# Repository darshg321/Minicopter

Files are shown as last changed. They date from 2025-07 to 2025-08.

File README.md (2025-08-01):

# Minicopter

A lightweight ESP-32 based drone capable of autonomous pathing, built for agility. Uses the GY-87 breakout board with a three-axis gyroscope + triaxial accelerometer + three-axis magnetic field + pressure. Charges a LiPo battery with USB-C and can be flashed with firmware.
Can be controlled with both pathing commands and bluetooth controls.

I made this project after getting inspiration from a different esp32 drone reel, and thought I could make that too
I've additionally always wanted to get into creating a from-scratch hardware project that includes microcontrollers and pcbs, and thought this was the perfect place to start

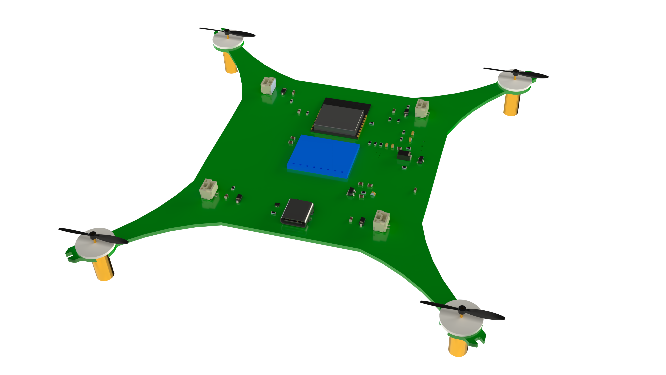
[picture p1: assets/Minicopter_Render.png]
cad


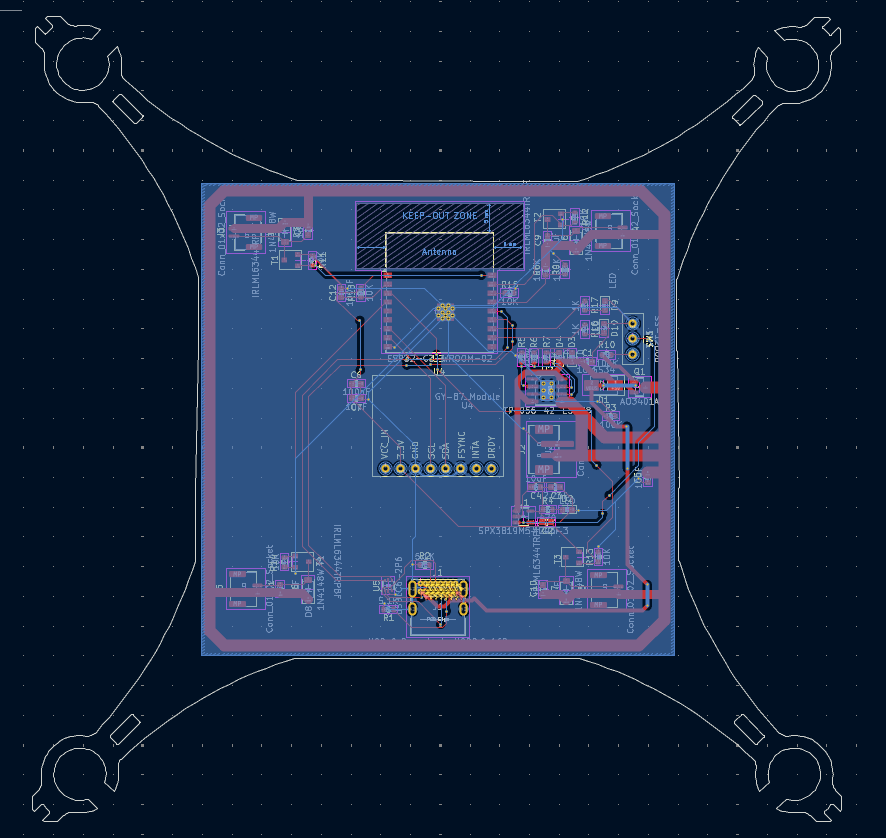
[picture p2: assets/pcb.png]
pcb


## Read the [JOURNAL.md](JOURNAL.md)

# BOM

| Value | Qty | Price (USD, approx) |
|---|-----|---|
| 10uF | 3 | 0.46 |
| 470pF | 1 | 0.4 |
| 2.2uF | 1 | 0.19 |
| 100nF | 2 | 0.14 |
| 10nF | 1 | 0.09 |
| 1uF | 4 | 0.05 |
| SS34 | 1 | 0.66 |
| LED | 5 | 1.39 |
| 1N4148W | 4 | 0.77 |
| USB_C_Receptacle_USB2.0_16P | 1 | 0.88 |
| Conn_01x02 | 1 | 1.39 |
| Conn_01x02_Socket | 4 | 0.70 |
| AO3401A | 1 | 0.46 |
| 5.1K | 2 | 0.45 |
| 100K | 4 | 0.2 |
| 470 | 1 | 0.28 |
| 1.2K | 1 | 0.61 |
| 1K | 4 | 0.2 |
| 10K | 6 | 0.19 |
| SS-12D00 | 1 | 1.39 |
| IRLML6344TRPBF | 4 | 1.08 |
| SPX3819M5-L-3-3 | 1 | 0.46 |
| TP4056-42-ESOP8 | 1 | 1.73 |
| ESP32-C3-WROOM-02 | 1 | 3.28 |
| GY-87_Module | 1 | 3.00 |
| USBLC6-2P6 | 1 | 0.46 |
| 3.7V 500mAh 902530 25C LiPo Battery | 3 | 12.68 |
| NewBeeDrone BDR Unicorn Edition Motors - 6mm Brushed Motors | 1 | 19.99 |
| NewBeeDrone Venom V2 Super Durable Propellers | 1 | 2.99 |
| Total (w/ shipping + tax) | | 138.15 |

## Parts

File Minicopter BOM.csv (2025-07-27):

Reference | Value | Footprint | Qty |  | Price (w/o shipping + taxes USD)
C1, C4, C5 | 10uF | Capacitor_SMD:C_0603_1608Metric | 3 | https://www.digikey.ca/en/products/detail/taiyo-yuden/LMK107BBJ106MALT/3662195 | 0.46
C2 | 470pF | Capacitor_SMD:C_0603_1608Metric | 1 | https://www.digikey.ca/en/products/detail/kemet/C0603C471J5GACTU/2200803 | 0.4
C3 | 2.2uF | Capacitor_SMD:C_0603_1608Metric | 1 | https://www.digikey.ca/en/products/detail/taiyo-yuden/TMK107ABJ225KA-T/2648986 | 0.19
C6, C12 | 100nF | Capacitor_SMD:C_0603_1608Metric | 2 | https://www.digikey.ca/en/products/detail/yageo/CC0603KRX7R7BB104/302822 | 0.14
C7 | 10nF | Capacitor_SMD:C_0603_1608Metric | 1 | https://www.digikey.ca/en/products/detail/kemet/C0603C103K5RACTU/411090 | 0.09
C8, C9, C10, C11 | 1uF | Capacitor_SMD:C_0603_1608Metric | 4 | https://www.digikey.ca/en/products/detail/samsung-electro-mechanics/CL10B105KP8NNNC/3887604 | 0.05
D1 | SS34 | Diode_SMD:D_SMA | 1 | https://www.digikey.ca/en/products/detail/onsemi/SS34/1052384 | 0.66
D2, D3, D4, D9, D10 | LED | LED_SMD:LED_0603_1608Metric | 5 | https://www.aliexpress.com/item/1005005431944057.html | 1.39
D5, D6, D7, D8 | 1N4148W | Diode_SMD:D_SOD-123 | 4 | https://www.digikey.ca/en/products/detail/smc-diode-solutions/1N4148W/6022450 | 0.77
J1 | USB_C_Receptacle_USB2.0_16P | Connector_USB:USB_C_Receptacle_GCT_USB4085 | 1 | https://www.digikey.ca/en/products/detail/gct/USB4085-GF-A/98596622 | 0.88
J2 | Conn_01x02 | Connector_JST:JST_PH_B2B-PH-SM4-TB_1x02-1MP_P2.00mm_Vertical | 1 | https://www.aliexpress.com/item/1005008131930144.html | 1.39
J3, J4, J5, J6 | Conn_01x02_Socket | Connector_JST:JST_GH_BM02B-GHS-TBT_1x02-1MP_P1.25mm_Vertical | 4 | https://www.aliexpress.com/item/1005005699355153.html | 0.7
Q1 | AO3401A | Package_TO_SOT_SMD:SOT-23 | 1 | https://www.digikey.ca/en/products/detail/alpha-omega-semiconductor-inc/AO3401A/1855773 | 0.46
R1, R2 | 5.1K | Resistor_SMD:R_0603_1608Metric | 2 | https://www.digikey.ca/en/products/detail/yageo/RC0603FR-075K1L/727268 | 0.45
R3, R8, R9, R10 | 100K | Resistor_SMD:R_0603_1608Metric | 4 | https://www.digikey.ca/en/products/detail/stackpole-electronics-inc/RMCF0603FT100K/1761112 | 0.2
R4 | 470 | Resistor_SMD:R_0603_1608Metric | 1 | https://www.digikey.ca/en/products/detail/te-connectivity-passive-product/CRGCQ0603F470R/8576286 | 0.28
R5 | 1.2K | Resistor_SMD:R_0603_1608Metric | 1 | https://www.digikey.ca/en/products/detail/panasonic-electronic-components/ERA-3AEB122V/14658566 | 0.61
R6, R7, R16, R17 | 1K | Resistor_SMD:R_0603_1608Metric | 4 | https://www.digikey.ca/en/products/detail/stackpole-electronics-inc/RMCF0603FT1K00/1761077 | 0.2
R11–R15, R18 | 10K | Resistor_SMD:R_0603_1608Metric | 6 | https://www.digikey.ca/en/products/detail/stackpole-electronics-inc/RMCF0603JT10K0/1758104 | 0.19
SW1 | SS-12D00 | SS-12D00:SS12-D00 | 1 | https://www.aliexpress.com/item/4001187999740.htmll | 1.39
T1, T2, T3, T4 | IRLML6344TRPBF | IRLML6344TRPBF:IRLML6344TRPBF | 4 | https://www.aliexpress.com/item/1005005586173911.html | 1.08
U1 | SPX3819M5-L-3-3 | Package_TO_SOT_SMD:SOT-23-5 | 1 | https://www.digikey.ca/en/products/detail/maxlinear-inc/SPX3819M5-L-3-3-TR/2472394 | 0.46
U2 | TP4056-42-ESOP8 | Package_SO:SOIC-8-1EP_3.9x4.9mm_P1.27mm_EP2.41x3.3mm_ThermalVias | 1 | https://www.aliexpress.com/item/1005009057944694.html | 1.73
U3 | ESP32-C3-WROOM-02 | RF_Module:ESP32-C3-WROOM-02 | 1 | https://www.digikey.ca/en/products/detail/espressif-systems/ESP32-C3-WROOM-02-N4/145530311 | 3.28
U4 | GY-87_Module | GY-87_Module:GY-87_Module | 1 | https://www.aliexpress.com/i/32668253323.html | 3 |  | Total (USD)
U5 | USBLC6-2P6 | Package_TO_SOT_SMD:SOT-666 | 1 | https://www.digikey.ca/en/products/detail/stmicroelectronics/USBLC6-2SC6Y/2819177 | 0.46 | Subtotal | 58.21
 | 2.54mm Headers |  | 1 | https://www.digikey.ca/en/products/detail/amphenol-cs-fci/10129378-910002BLF/7915958 | 1.64 | NewBeeDrone | 24.17
 | 3.7V 500mAh 902530 25C LiPo Battery |  | 3 | https://www.aliexpress.com/item/1005007016796736.html | 12.68 | Digikey | 20
 | NewBeeDrone BDR Unicorn Edition Motors - 6mm Brushed Motors |  | 1 | https://newbeedrone.com/collections/drone-motors/products/newbeedrone-bdr-unicorn-edition-motors-6mm-brushed-motors | 19.99 | Aliexpress | 25.77
 | NewBeeDrone Venom V2 Super Durable Propellers 31mm -0.8mm Shaft |  | 1 | https://newbeedrone.com/collections/drone-propellers/products/newbeedrone-venom-v2-super-durable-propellers-31mm-0-8mm-shaft4ccw-4cw | 2.99 | Taxes | 10
 |  |  |  |  | 58.21 |  | 138.15

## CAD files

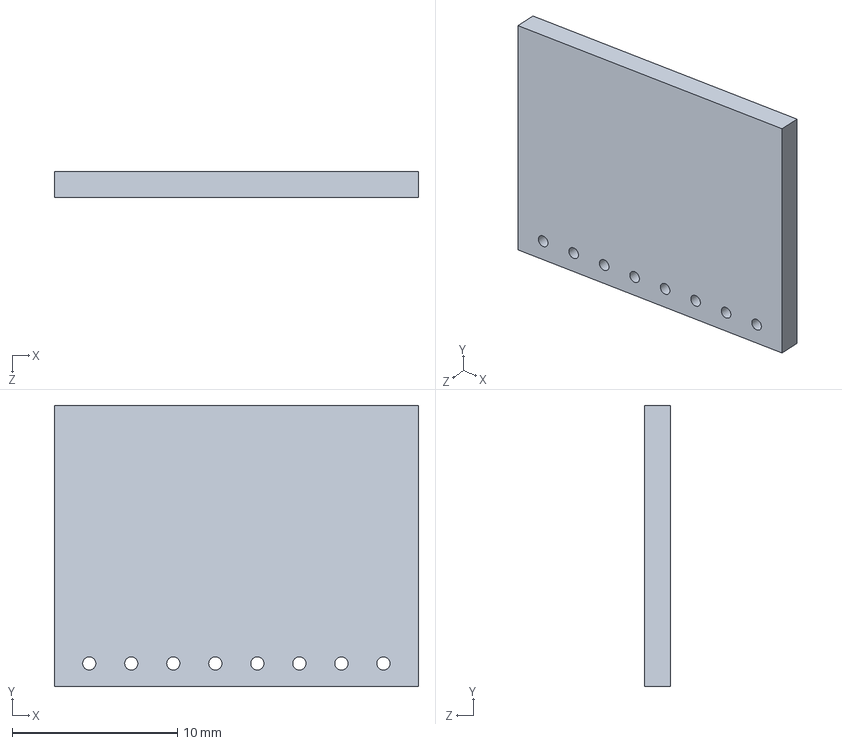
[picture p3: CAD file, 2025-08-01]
cad/GY-87.SLDPRT
22.0 x 17.0 x 1.60 mm

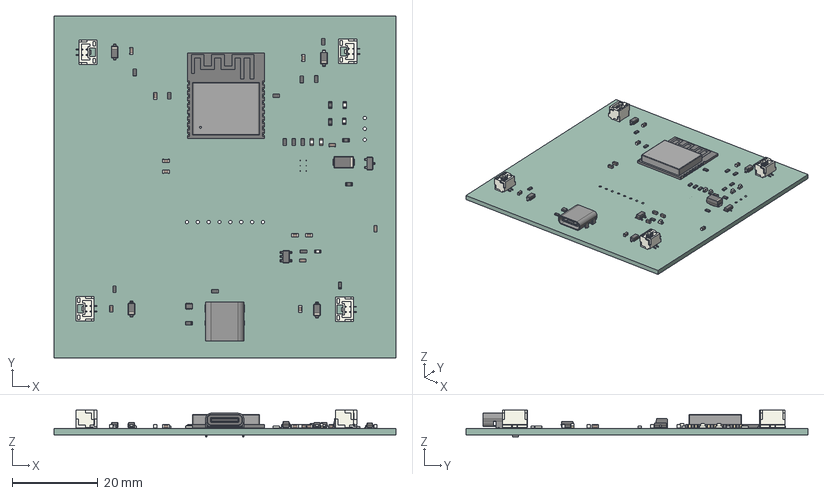
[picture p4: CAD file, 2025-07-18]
pcb/Minicopter.step
80.0 x 80.0 x 6.31 mm
D_SOD-123 x 4
JST_GH_BM02B-GHS-TBT_1x02-1MP_P1.25mm_Vertical x 4
R_0603_1608Metric x 18
ESP32-C3-WROOM-02
C_0603_1608Metric x 12
D_SMA
SOT-23-5
LED_0603_1608Metric x 5
SOT-666
SOT-23
USB_C_Receptacle_GCT_USB4085
Minicopter_PCB

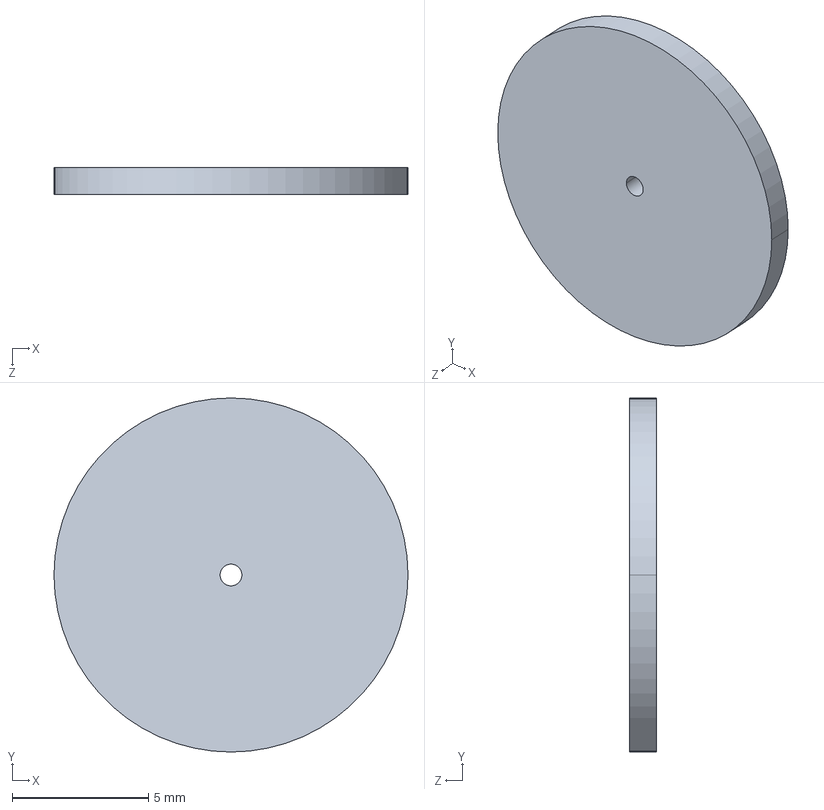
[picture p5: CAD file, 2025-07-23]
production/motor_attachment.STEP
13.0 x 13.0 x 1.00 mm

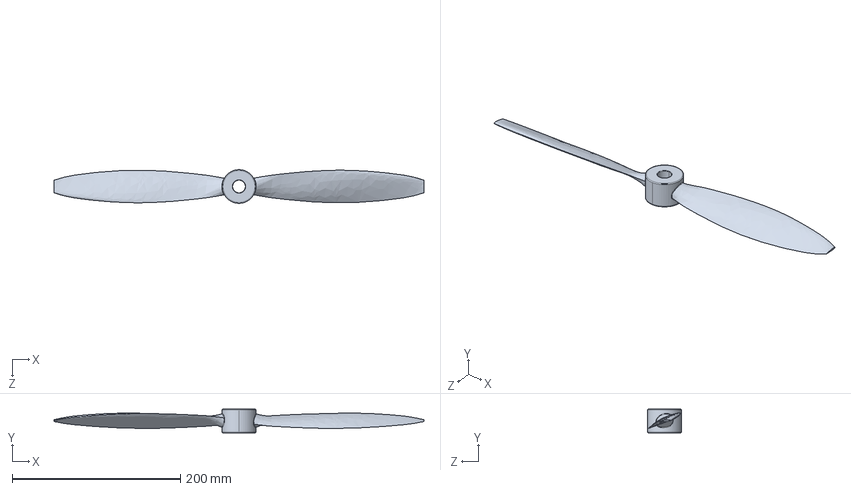
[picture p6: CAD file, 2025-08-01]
cad/BLDC Propeller.STEP
440.0 x 28.0 x 40.0 mm

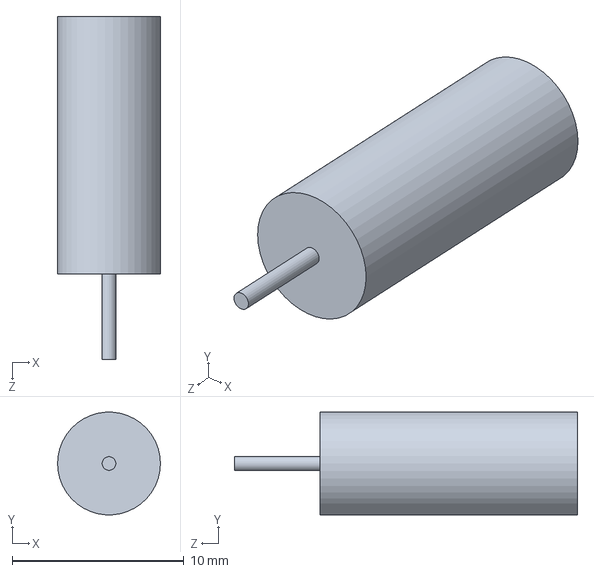
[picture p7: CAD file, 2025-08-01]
cad/Motor.SLDPRT
6.00 x 5.98 x 20.0 mm

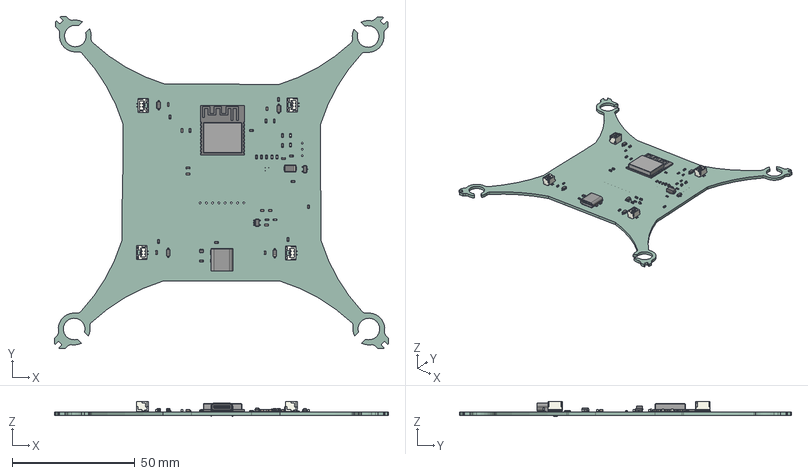
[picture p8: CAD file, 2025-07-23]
cad/Minicopter_PCB.step
136.1 x 135.4 x 6.31 mm
D_SOD-123 x 4
JST_GH_BM02B-GHS-TBT_1x02-1MP_P1.25mm_Vertical x 4
R_0603_1608Metric x 18
ESP32-C3-WROOM-02
C_0603_1608Metric x 12
D_SMA
SOT-23-5
LED_0603_1608Metric x 5
SOT-666
SOT-23
USB_C_Receptacle_GCT_USB4085
Minicopter_PCB

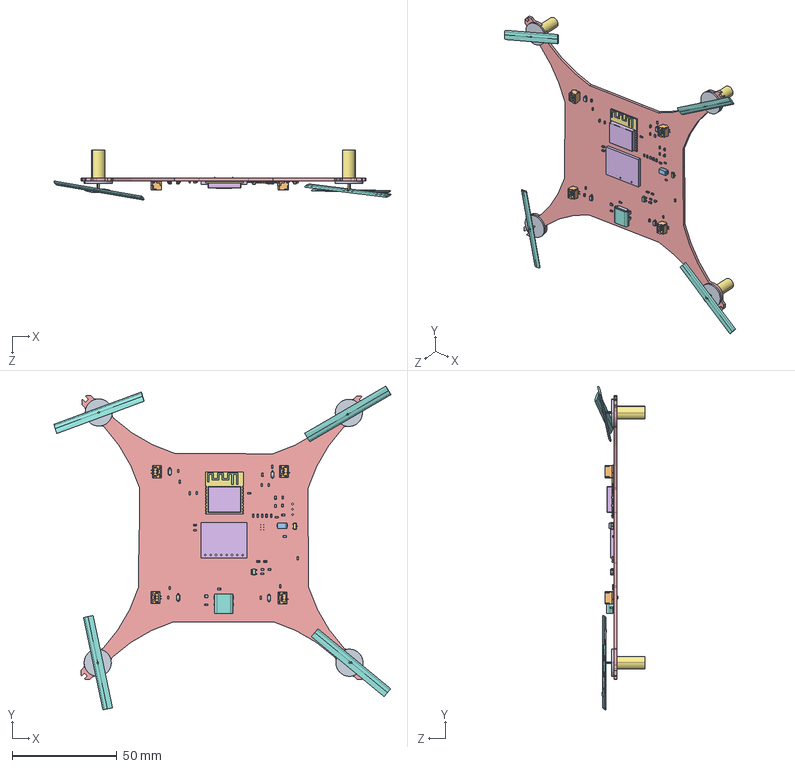
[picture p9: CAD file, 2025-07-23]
cad/Minicopter.STEP
160.8 x 154.4 x 24.1 mm
D_SOD-123 x 4
JST_GH_BM02B-GHS-TBT_1x02-1MP_P1.25mm_Vertical x 4
R_0603_1608Metric x 18
ESP32-C3-WROOM-02
C_0603_1608Metric x 12
D_SMA
SOT-23-5
LED_0603_1608Metric x 5
SOT-666
SOT-23
USB_C_Receptacle_GCT_USB4085
Minicopter_PCB
GY-87
Motor x 4
Propellers x 4
motor_attachment x 4

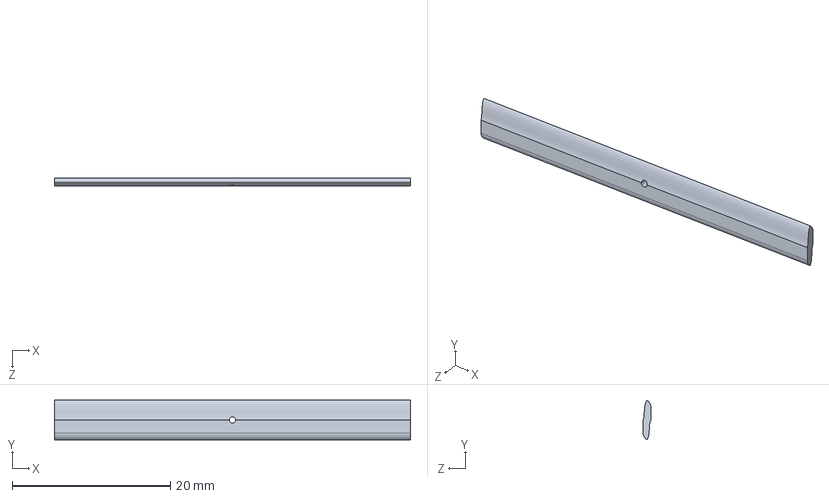
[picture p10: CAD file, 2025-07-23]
cad/Propellers.SLDPRT
45.0 x 5.00 x 1.00 mm

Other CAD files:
cad/motor_attachment.SLDPRT
cad/CirPattern1_1.SLDPRT
cad/USB_C_Receptacle_GCT_USB4085.SLDPRT
cad/D_SOD-123.SLDPRT
cad/SOT-23-5.SLDPRT
cad/C_0603_1608Metric.SLDPRT
cad/D_SMA.SLDPRT
cad/SOT-666.SLDPRT
cad/ESP32-C3-WROOM-02.SLDPRT
cad/JST_GH_BM02B-GHS-TBT_1x02-1MP_P1.25mm_Vertical.SLDPRT
cad/BLDC Propeller.SLDASM
cad/LED_0603_1608Metric.SLDPRT
cad/Minicopter.SLDASM
cad/Minicopter_PCB.SLDPRT
cad/R_0603_1608Metric.SLDPRT
cad/SOT-23.SLDPRT

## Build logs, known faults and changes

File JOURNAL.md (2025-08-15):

## time: 35 hours

## july 6 & 7

got inpsiration for this project from this reel: https://www.instagram.com/p/DKDFd3nS-c8/
other inspiration: https://circuitdigest.com/microcontroller-projects/DIY-wifi-controlled-drone

goals of this drone:

- can fly reliably
- wireless controller
- PID control
- 4 ish minute flight time
- usb c charging
- can have semi reliable autonomous paths (can create one to takeoff, fly from my room to couch, and land, reliably)

the guy uses NewBeeDrone BDR GOLD Edition - 6mm Brushed Motor, so i'll be basing my design off of these motors

shoutout to this blog article for being quite helpful in esp selection: https://eitherway.io/posts/esp32-buyers-guide/
i will go with the esp32-c3-wroom-02 for its bluetooth 5.0 and efficiency

parts v1:
NewBeeDrone BDR GOLD Edition - 6mm Brushed Motor (https://newbeedrone.com/products/newbeedrone-bdr-gold-edition-6mm-brushed-motor)
Bitcraze Crazyflie Nano Quadcopter Replacement Propellers (https://ca.robotshop.com/products/crazyflie-nano-quadcopter-replacement-propellers)
Fytoo 5pcs 3.7V 500mAh 25C Li Battery (https://www.amazon.ca/dp/B0794ZPVSX)
ESP32-C3 (https://www.digikey.ca/en/products/detail/espressif-systems/ESP32-C3/14115579)
GY-87 (https://x2robotics.ca/gy-87-10dof-mpu6050-hmc5883l-bmp180-sensor-module)
TYPE-C-31-M-12 (https://lcsc.com/product-detail/USB-Type-C_Korean-Hroparts-Elec-TYPE-C-31-M-12_C165948.html)
TP4056 (https://www.aliexpress.com/item/1005005838857868.html)
SPX3819M5-L-3-3 (https://www.aliexpress.com/item/1005007348027539.html)
IRLZ44N (https://www.aliexpress.com/item/1005006228628494.html)

- figure out how to implement tp4056 with battery protection or figure out if its not necessary
- figure out how to add breakout board to custom pcb

components left: motor driver, battery charge terminal, controller components (oled screen etc)

+4 hours; lot of research :( 

making a choice not to use usb uart bc im using esp32 c3 and will just use the native usb support

# schematics:

## july 8th

components:
usb_c_receptable_usb2.0_16p
AO3401A
SS34
SPX3819M5-L-3-3
4 capacitors, 3 resistors, and 1 led

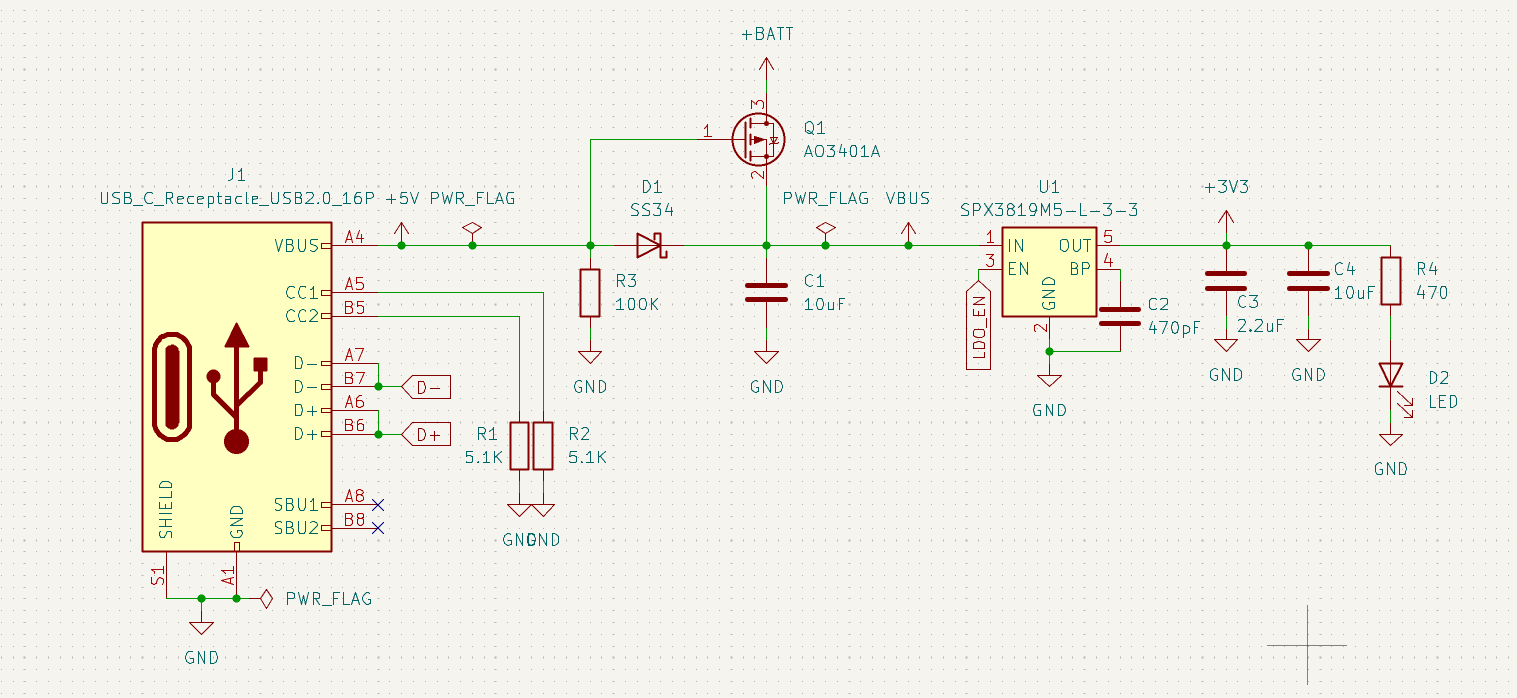
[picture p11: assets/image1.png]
power


circuit explanation for later me:
- cc1 and cc2 have resistors to let chargers know to supply power, not take in power
- vbus is 5v, the goal of the circuit is to convert it into stable 3v
- power goes to ss34 where cathode is toward vbus, prevents reverse current
- r3 ensures mosfet is on when usb isnt connected due to gnd connection, and turns mosfet off when usb is connected
- ao3401A (mosfet) allows for battery power when usb isnt connected
- EN is to turn the ldo on, which acts as the power switch for the entire device
- BP is for noise reduction, adding a capacitor does this
- two more capaicitors to add stabalization on the 3v3 rail, connected in parallel and will supply voltage in drops
- green led for on status

components:
TP4056
2 resistor, 3 resistor, 1 capacitor
51005-0200 molex female housing

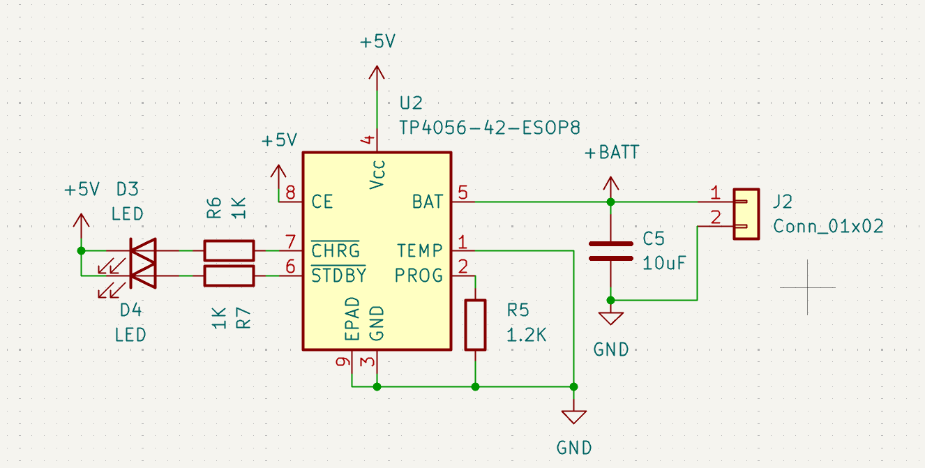
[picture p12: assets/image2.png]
battery


circuit explanation: 
- power comes from vcc
- ce turns on charging, connected to 5v so always charging
- epad is for cooling
- temp is for temp monitoring (not doing that)
- prog is to set charging amps (1amp at 1.2k resistor)
- capicitor smooths out charging

third schematic: on/off and voltage monitoring (battery control)

components:
3 resistors
MST22D18G2_125 (https://www.amazon.ca/100Pcs-MSS22D18-Miniature-Switch-Handle/dp/B093LBLK6D)

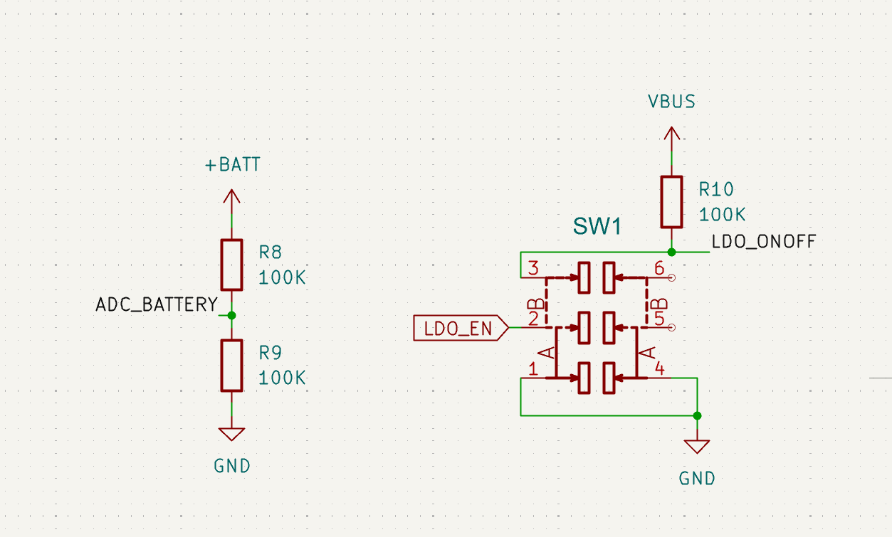
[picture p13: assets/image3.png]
batterycontrol


+6 hours

## july 9th

circuit explanation:
- battery capacity is measured by the voltage divider, linking to an adc pin
- when switch is toggled, it either connects ldo's en to gnd (off), or to vbus via r10
- r10 is there to not short the circuit when untoggled (pull up resistor)

fourth schematic: microcontroller

components: 
- esp32-c3-wroom-02
- 2 resistor, 1 capacitor

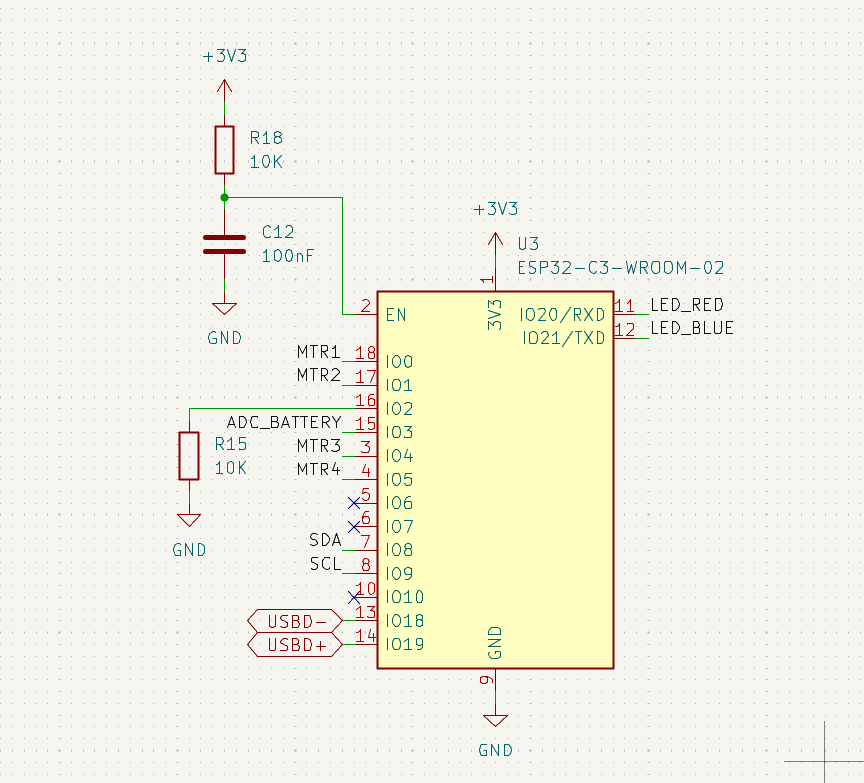
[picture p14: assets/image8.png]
microcontroller


circuit explanation:
- en must be HIGH to boot, pull up resistor and capacitor for stability
- io2 is for boot and optionally has a pull down resistor
- io6, 7, and 10 are for firmware and cannot be connected
- io20/21 are rxd and txd and supposed to be for uart serial communication, but since im using native usb ill be controlling leds with them
- io3 works for adc
- io18/19 are usb for the esp32-c3-wroom-02

fifth schematic: sensor
unfortunately the mpu6050 seems to only be in qfn form (and discontinued) and since i dont have the tools to solder that, i'll be using the gy-87 module
links that are helpful w this:
https://docs.sunfounder.com/projects/elite-explorer-kit/en/latest/basic_projects/09_basic_gy87.html
https://www.reddit.com/r/PrintedCircuitBoard/comments/b704j7/how_to_connect_breakout_board_with_a_pcb/
https://electropeak.com/learn/interfacing-gy-87-10dof-imu-mpu6050-hmc5883l-bmp085-module-with-arduino/
https://5.imimg.com/data5/LF/FE/MY-1833510/gy-87-10dof-mpu6050-hmc5883l-bmp180-sensor-module.pdf

gy87 symbol: 
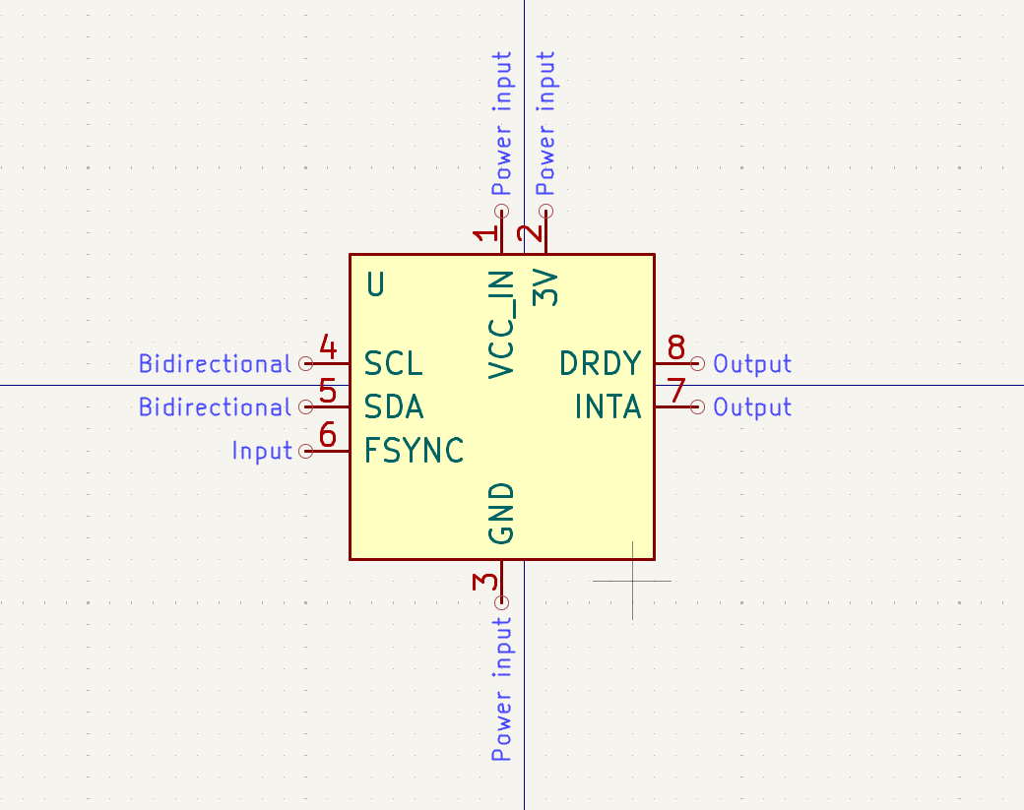
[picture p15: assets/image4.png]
gy87 symbol


components:
- gy87
- 2 capacitor

connections:
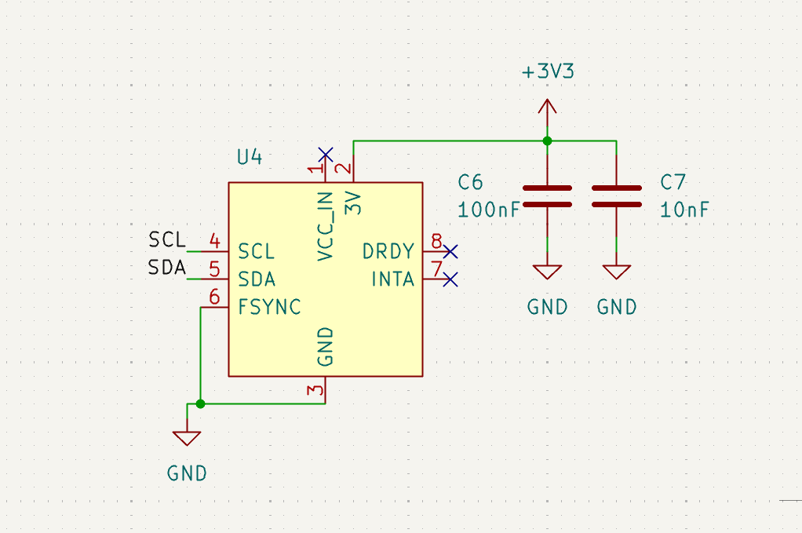
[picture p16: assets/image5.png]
sensor


circuit explanation:
- scl and sda go to the pins on esp32, dont need pull up resistors or 3v because the breakout board already has that
- dont use vcc_in, drdy, and inta
- fsync connects to gnd because its an output pin unlike the other input pins, and so may pick up on random noise and so has to be connected to gnd
- breakout board likely already has decoupling capacitors for the power, but might as well add them anyways for ensured reliability

+6 hours

## july 10th

sixth schematic: motor drivers

components:
- 4 IRLML6344TRPBF
- 4 resistor
- 4 1N414BW

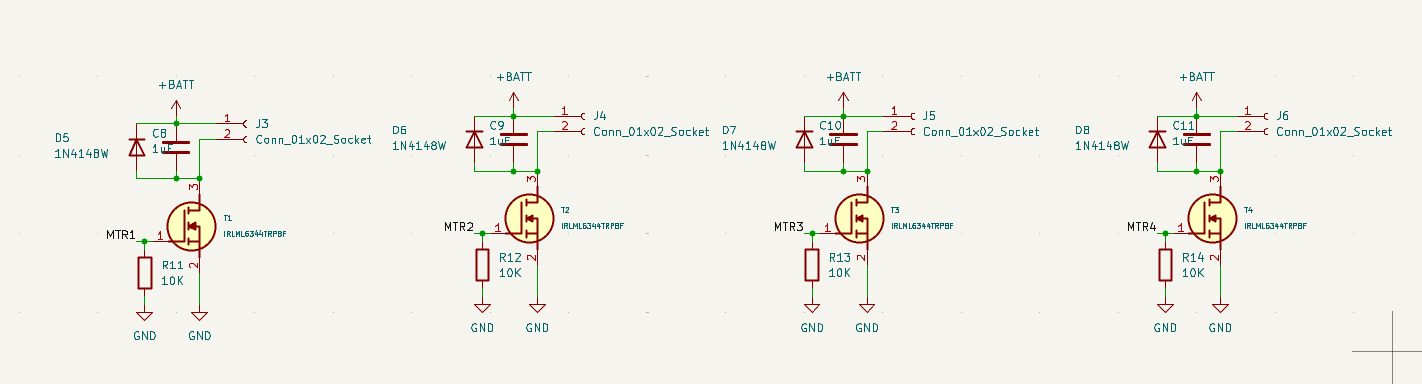
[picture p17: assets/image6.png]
motor drivers


circuit explanation:
- pin 1 is the gate on the mosfet, pin 3 is the drain, pin 2 is the source
- when pin 1 of the mosfet is turned on by the microcontroller, the switch is on and the current can flow from the battery to gnd
- this allows the motor to spin because it connects the motors negative terminal to gnd
- when the mosfet is closed, the motor cannot spin because it only has positive terminal plugged into the battery

seventh schematic: status leds

components:
- 2 leds
- 2 resistors

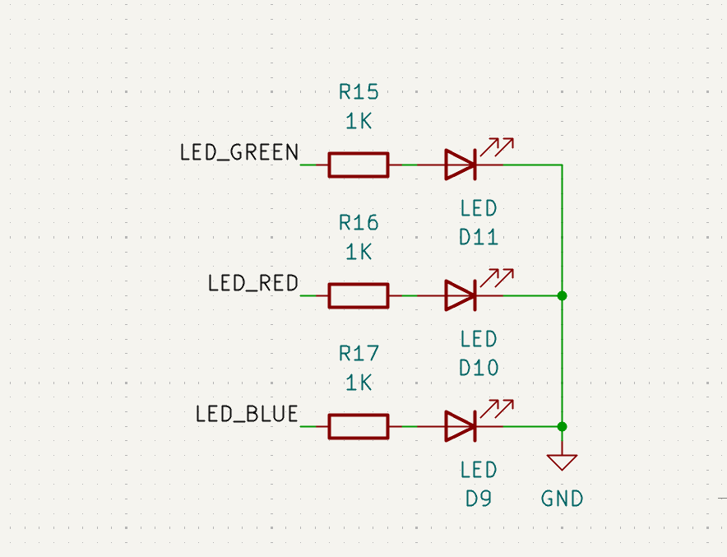
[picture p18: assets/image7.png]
status leds


finished
now for errors :(
fixed errors, apparently net labels dont work across sheets so made it all hierarchical lables

finished root schematic
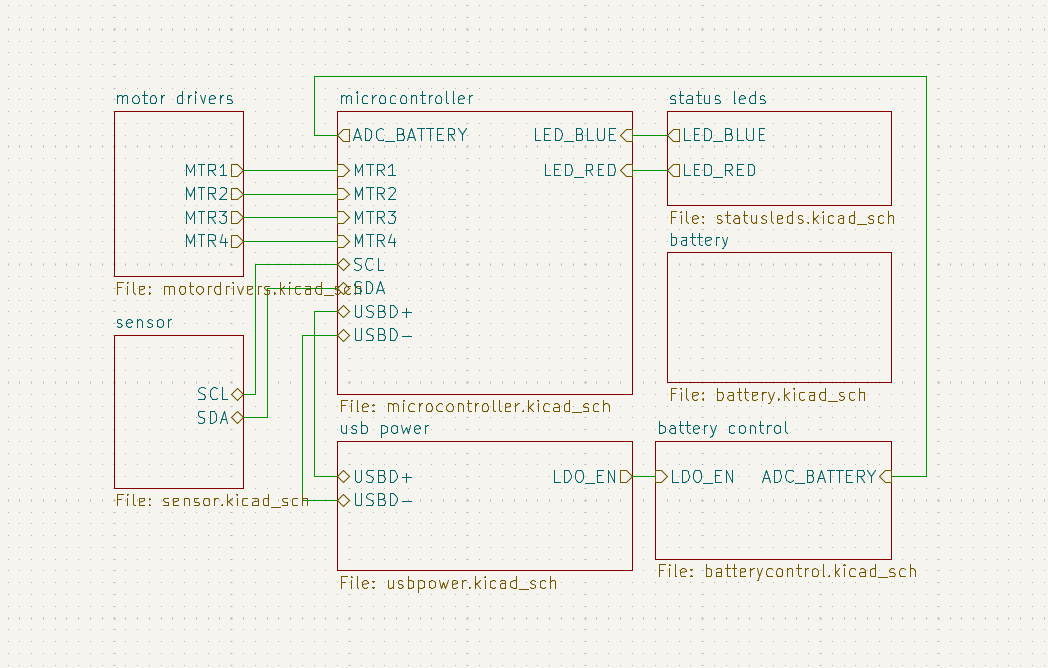
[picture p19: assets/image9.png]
finished root schematic


footprint notes:
using 603 standard footprints for mostly everything

GY-87 footprint
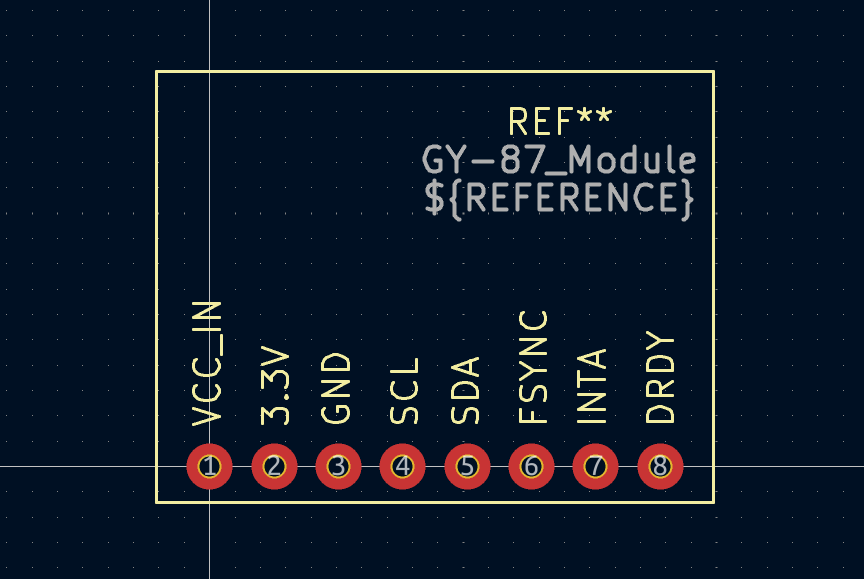
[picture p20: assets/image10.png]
gy-87 footprint


swapped out the original switch with a different one bc the other one is impossible to source
ss12-d00 footprint: (also made the schematic)
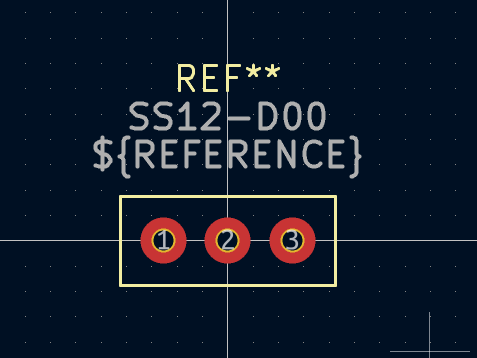
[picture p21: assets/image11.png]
ss12-d00


irlml6344TRPBF footprint
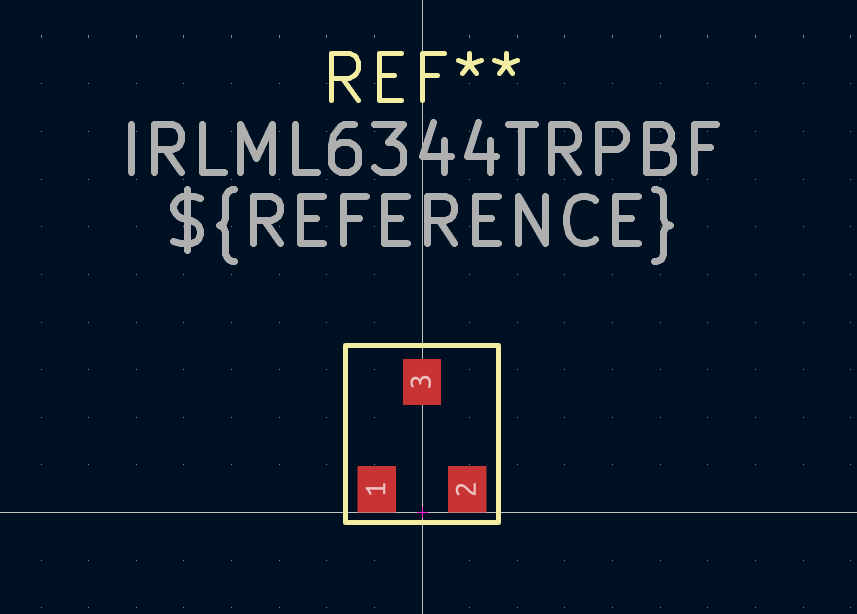
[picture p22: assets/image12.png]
irlml6344TRPBF

requirement: leave >= .2mm clearance between silkscreen and pads

zero errors/warnings in erc and updating pcb from schematic !!

+4 hours

# bom making:
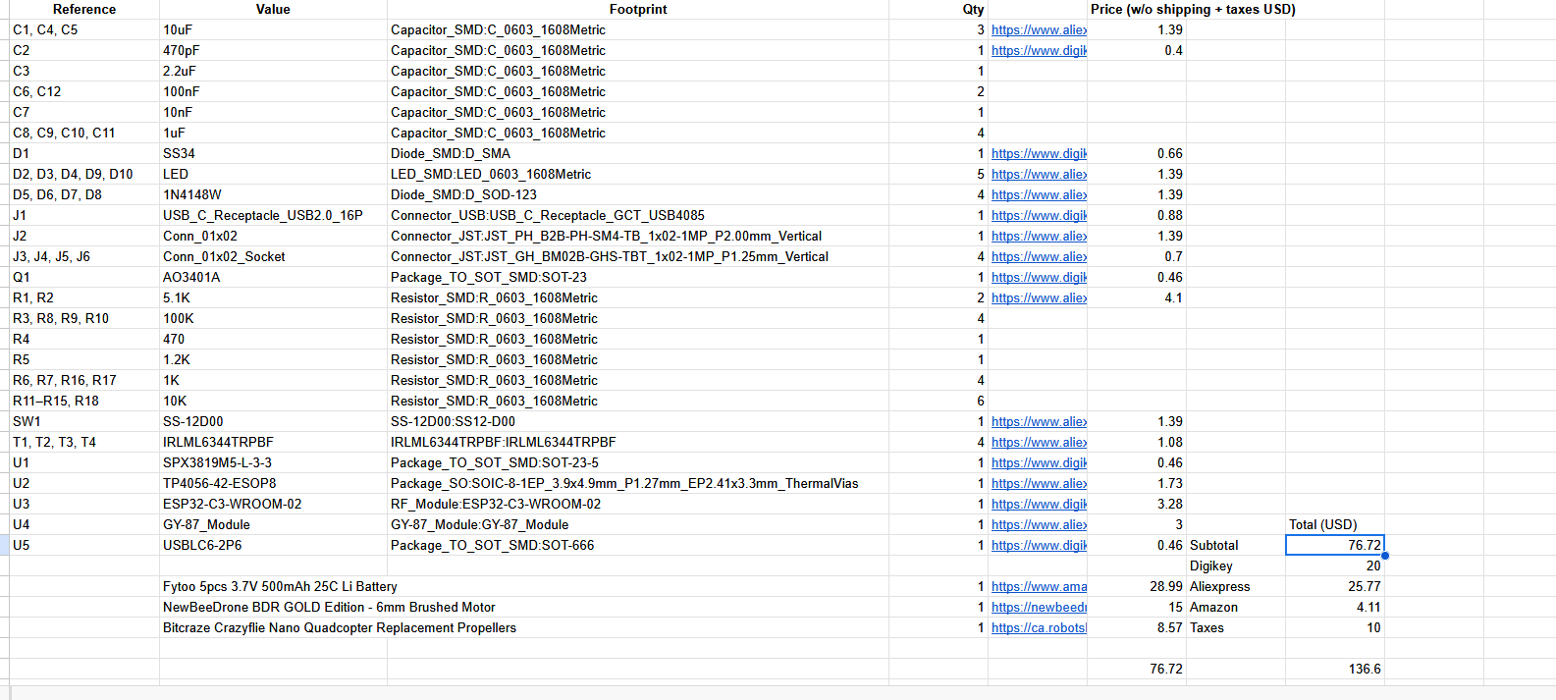
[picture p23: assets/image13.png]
bom


+1 hour

# pcb

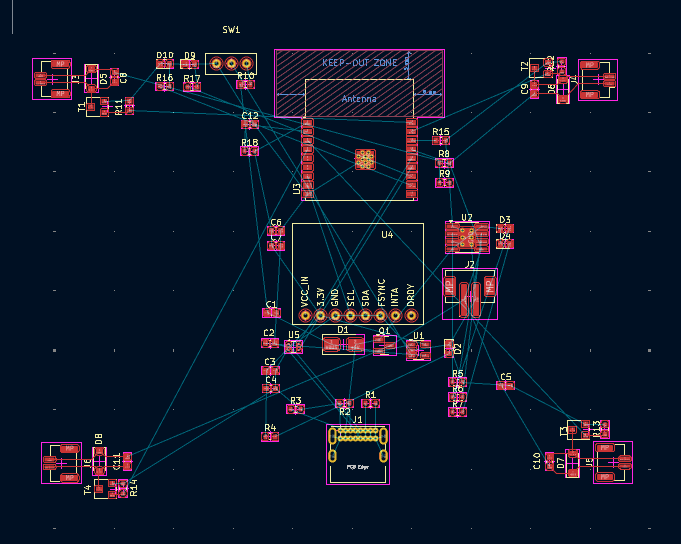
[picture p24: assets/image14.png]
pcb1
rough positioning: 

doing a 2 layer pwr + signal / gnd pcb
this is because 4 layer is complicated and probably unnecessary

progress:
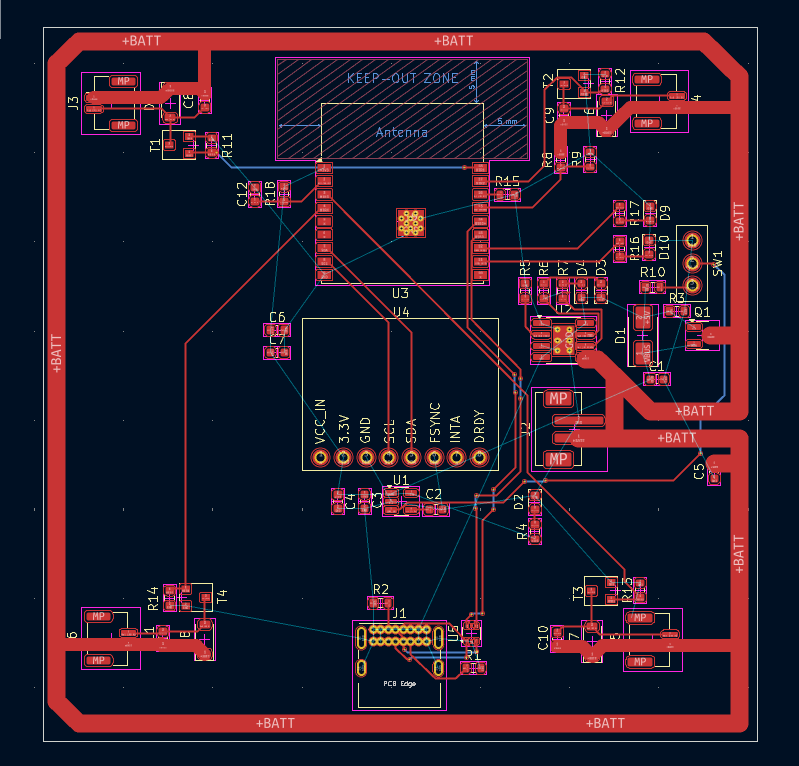
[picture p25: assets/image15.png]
pcb2


note: vbus is the unprotected power rail directly from usb, while 5v is the protected one
this doesnt make sense with my current schematic cause then the vbus isnt really doing anything, its just connected to the diode
the 5v from the usb is the one powering everything anyways
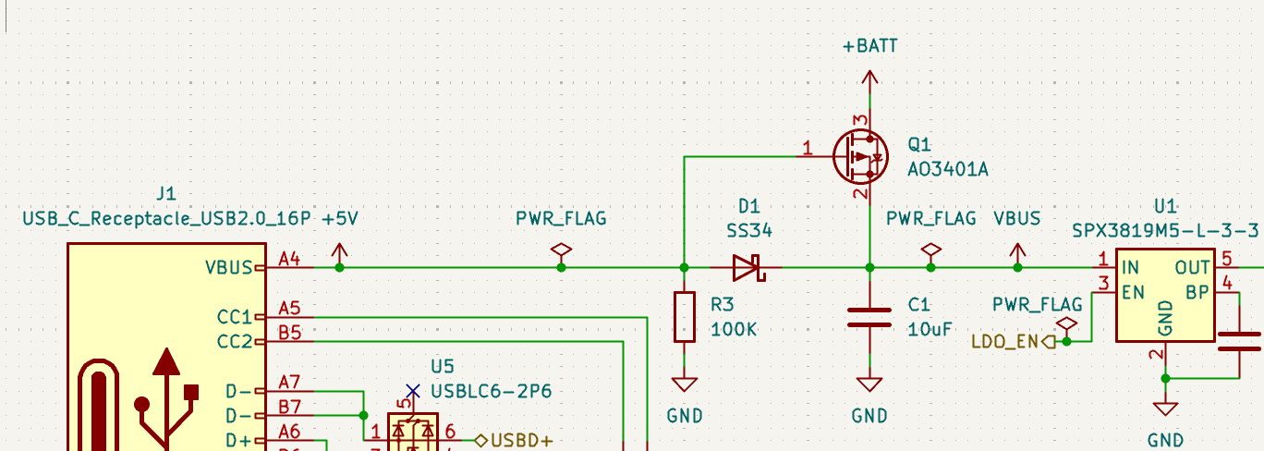
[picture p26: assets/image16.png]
schem

so swapping the 5v and vbus flags in the schematic above to correctly reflect the unprotected 5v from the usb going to the diode, becoming protected

+3 hours

## july 15th - 17th

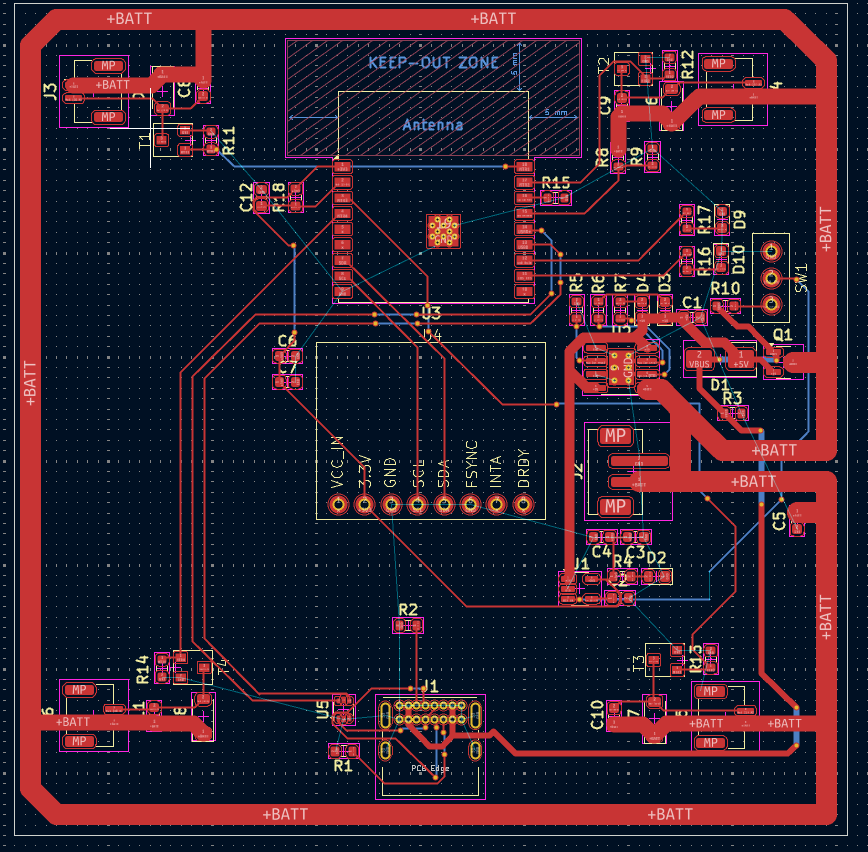
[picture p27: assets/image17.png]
pcb 3

done with everything except ground layer

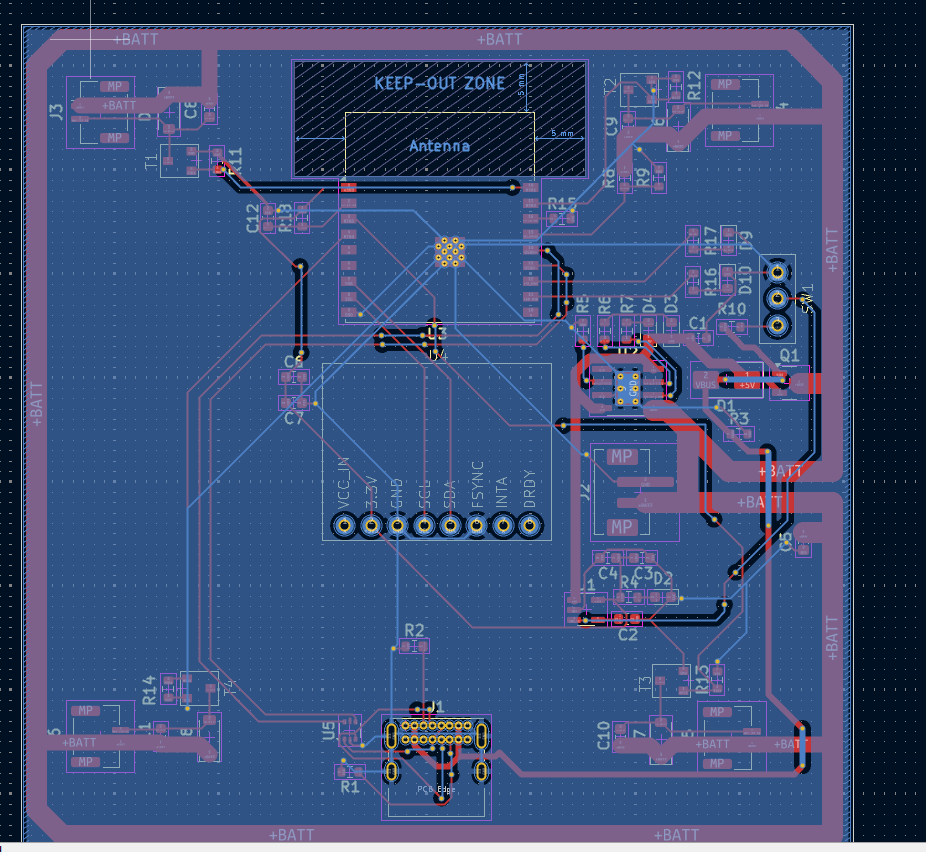
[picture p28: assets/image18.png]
pcb 4

with gnd layer

box:
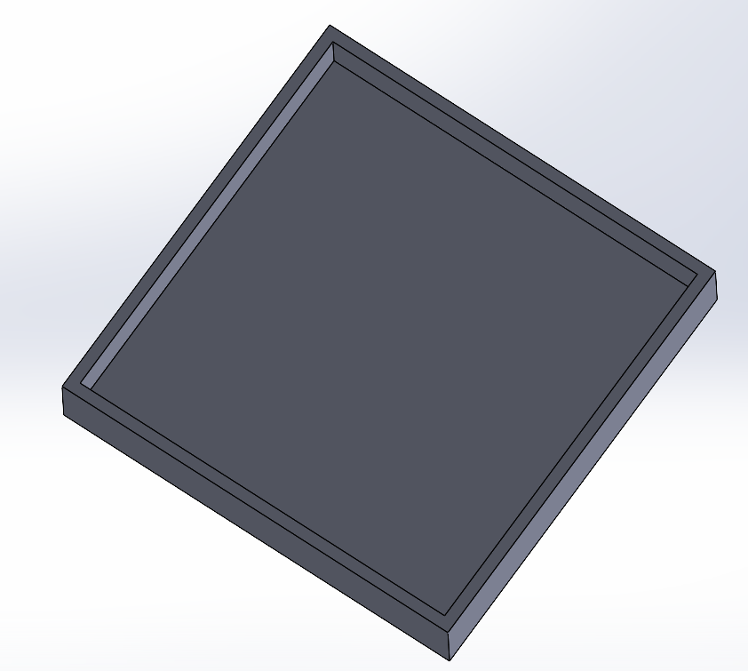
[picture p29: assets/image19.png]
box


+2 hours

## july 18th

slight pivot, i was going to cad a 3d printed case for this but realized that the motors are actually not that powerful, and a 3d printed case might be too heavy
theres also no reason to have a case if i can just use the pcb, its seemingly stable enough
the only issue would be vibrations potentially affecting the hardware, but since this doesnt seem to be a huge problem in the litewing, it should be fine for my project
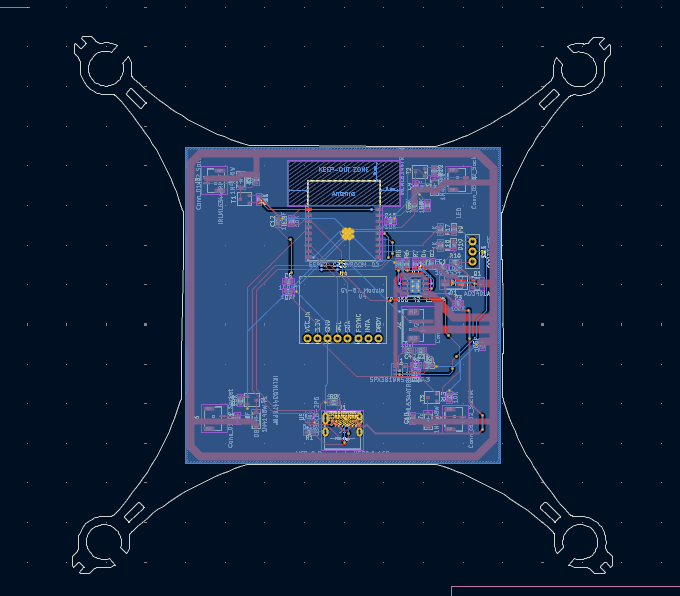
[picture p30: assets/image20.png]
new pcb


+1 hour

# firmware

using micropython as circuit python is apparently bad for pwm, i dont want to use arduino c, and no one uses espressif's thing probably

mpu6050 driver: https://github.com/nickcoutsos/MPU-6050-Python
(also requires smbus package, replaced that with smbus3)

really basic firmware code, cant really do more without the microcontroller

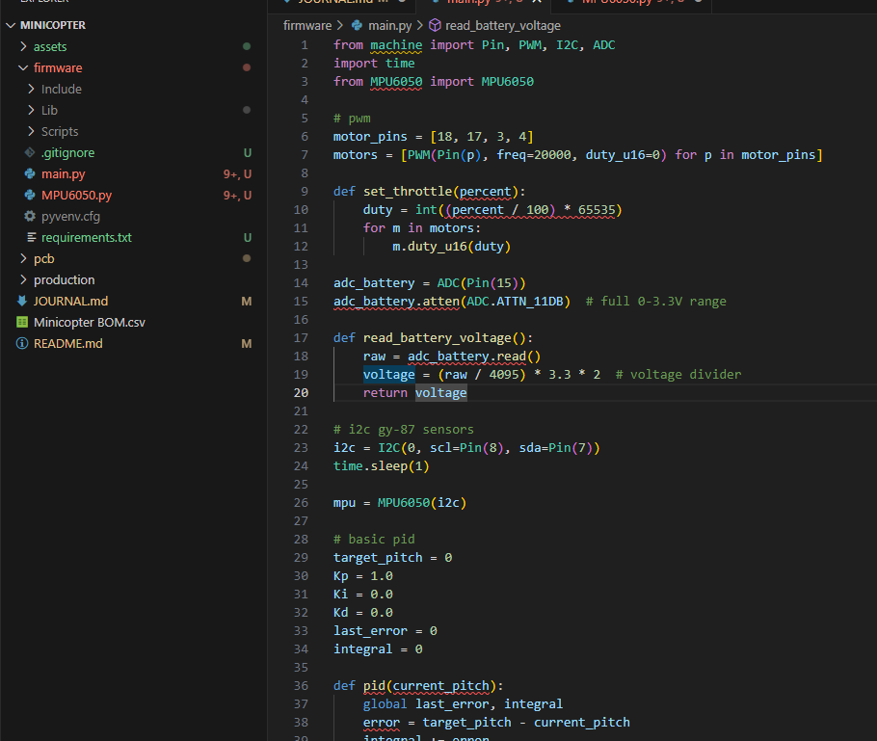
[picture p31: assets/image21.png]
firmware1


+2 hours

generating production files

## july 22

minor issues to fix, also need to add a cad
fixed thermal relief issue by making GND on usb receptacle have solid thermal relief, which shouldnt be an issue because i wont be hand soldering this
deleted holes on edge outline which is unnecessary
used heal shape with edge cuts because apparently outline wasnt closed off  (whyd it let me export as a gerber then bruh)

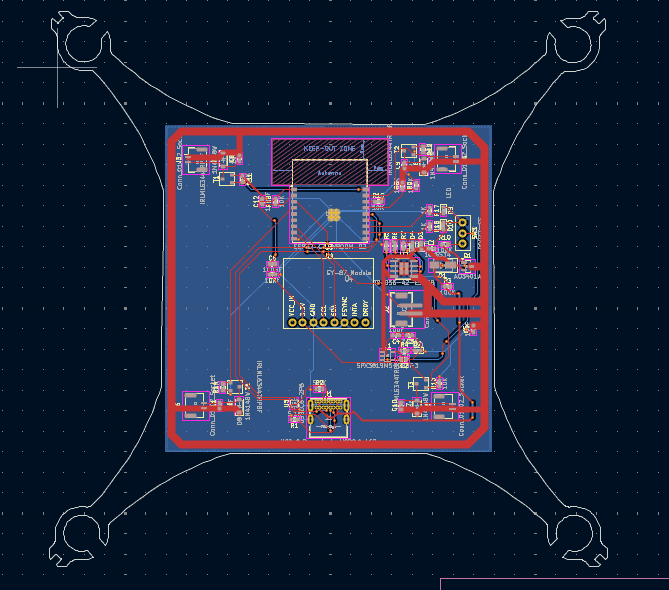
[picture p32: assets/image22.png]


# CAD

gy87 breakout board cad
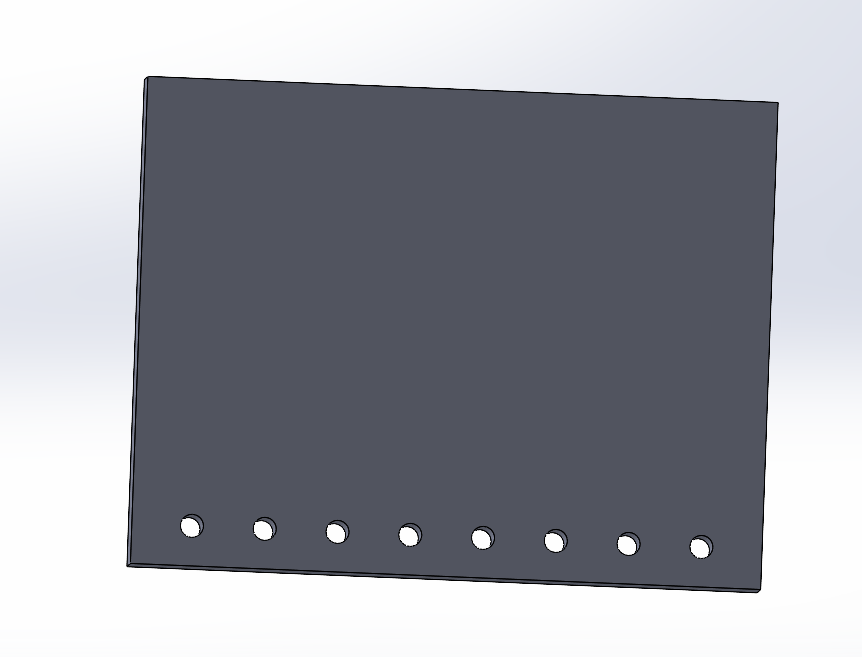
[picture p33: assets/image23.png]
gy87 cad


motor cad
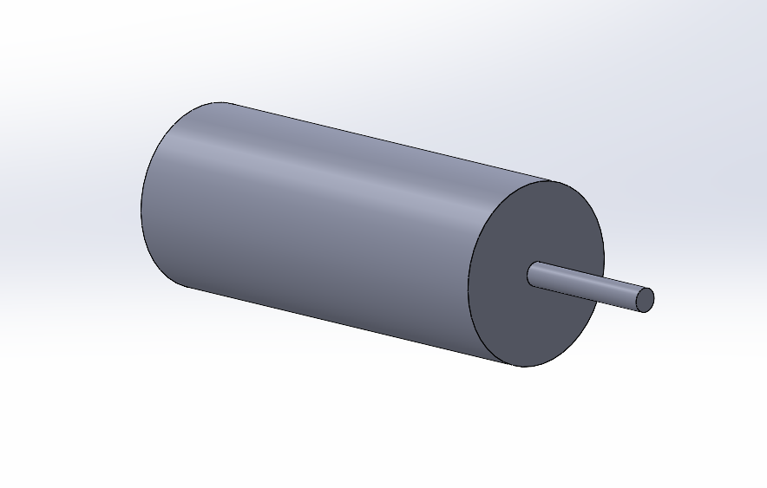
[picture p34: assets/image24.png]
motor cad


propellers cad
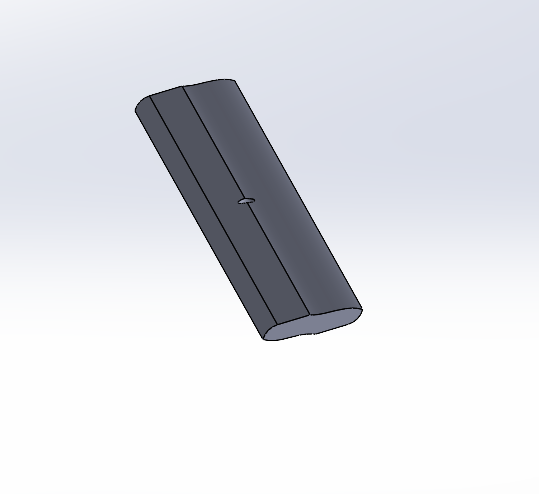
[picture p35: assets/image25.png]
propellers cad


motor attachment cad
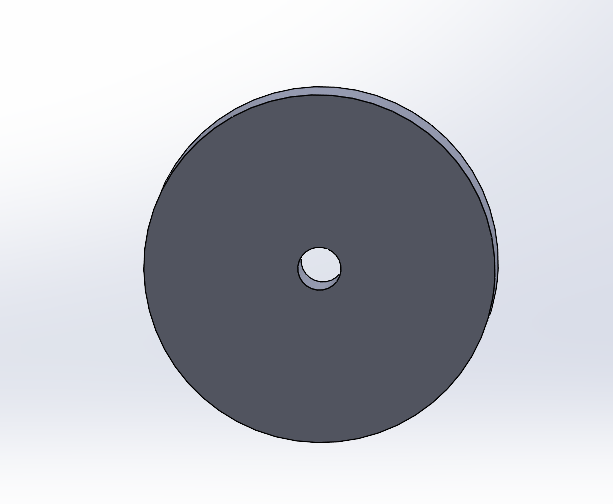
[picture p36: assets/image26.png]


full assembly cad
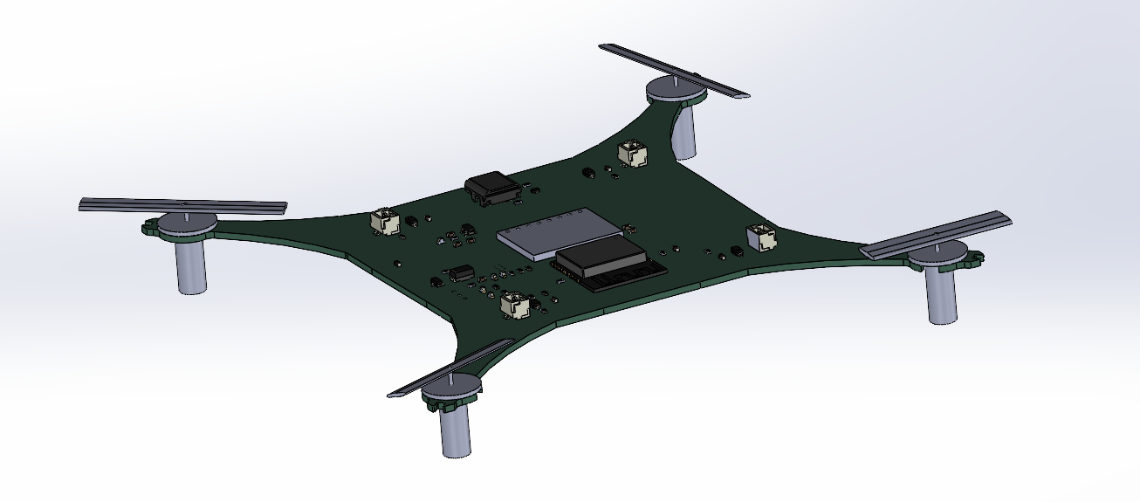
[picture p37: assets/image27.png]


+6 hours

## july 24-28

made changes to BOM to use more digikey, and SMD components (oops)
firmware: added pathing which while can't be very accurate without the physical build, should hopefully be a reasonable base
used https://github.com/hashky/bmp180-circuitpy for bmp driver, big shoutout to that guy, porting it from adafruit took a lot of math

+4 hours

## july 29

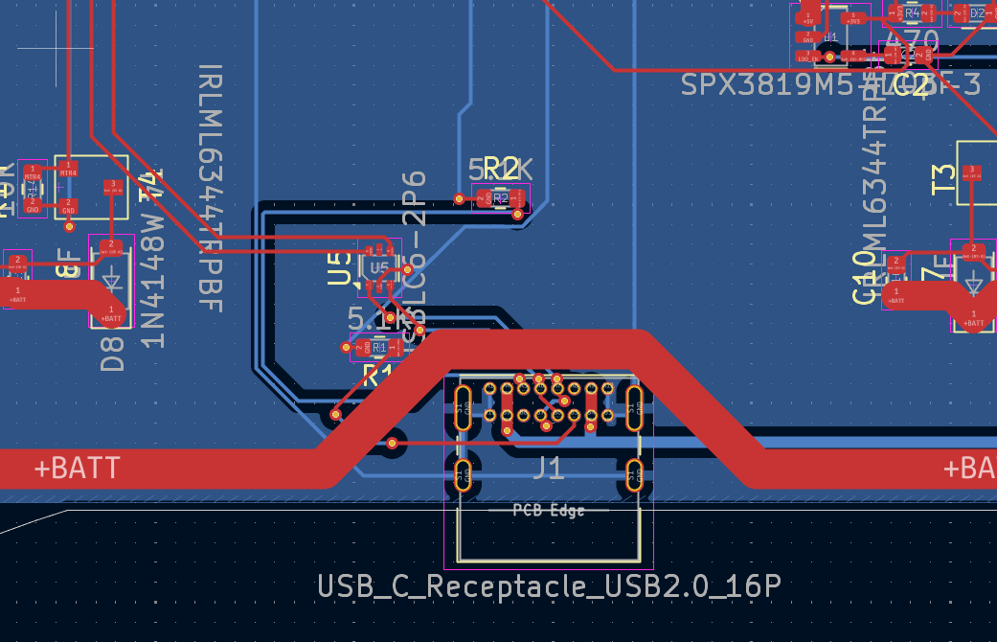
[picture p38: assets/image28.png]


fixed the receptacle not being at the edge

## aug 5th

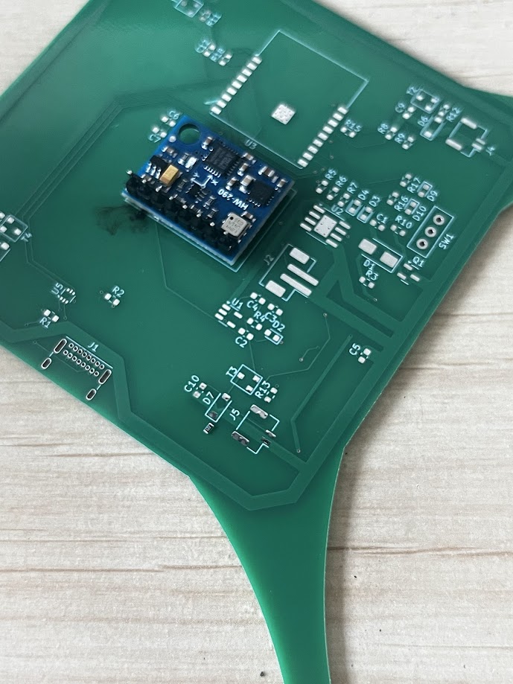
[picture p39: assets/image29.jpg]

pcb got here, starting assembling

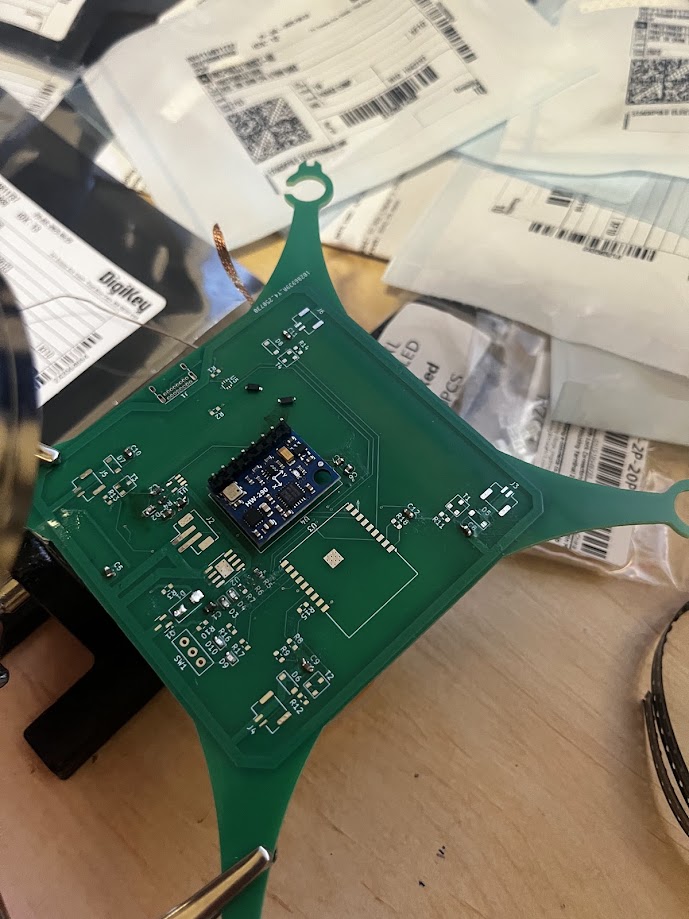
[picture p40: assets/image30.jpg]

some progress, soldered resistors and some other stuff

+3 hours

## aug 6th


done soldering components (besides motors)
need to now troubleshoot

+3 hours

## aug 7th


trying to figure out how to power with battery as jst housing is not what i expected


soldered wire to power with battery, but this isnt consistent

fixed some connections as they werent really working
+3 hours

## aug 12th

fixed powering with battery by soldering headers on to the pads, which i can connect the battery to for correct power

currently troubleshooting with only battery:
without usb the 5v rail is actually 3.86v which makes sense
the ldo is supply 0.6v which is likely because i used a 100k resistor on my ldo switch (which actually works), so the ldo en is 0.3v and therefore its probably disabled

changing r10 to a 10k resistor and trying again
didnt work, by adding a resistor connecting vin to en the en is now high, but output is still not 3.3v, its 2.6v
+4 hours

## aug 13th

troubleshooting by testing everything with multimeter, and found that the issue is definitely the ldo, and the usb power also doesnt actually work either

after a while of trying to figure out how to power it, found i have a breadboard power supply, so im powering it with a alkine battery and the power supply, and soldered to the 3v3 rail at the mcu and gnd



this fixed it, with multimeter testing it has proper 3v3 power

+4 hours

## aug 14th

esp should now be powered properly, so i need to flash firmware, which isnt working
multimeter tested everything, and with analyzing the board i found the usb cc pull downs werent soldered properly, so i resoldered them, and the usb does now power 5v properly to the 5v rail, but since i removed my ldo i still need to use the breadboard power supply for now

i still cant flash firmware, since i didnt put boot buttons i have to manually pull low for flashing, but it still doesnt connect to my computer
after looking at the circuit more, i found that the usblc i used was probably not soldered properly
unfortunately the pads are very very small, which i didnt realize when designing so i need to figure out how to connect the data pads together since its too small for wires, and the usblc ic seems to be too big for the pads even though i used the correct footprint

+4 hours

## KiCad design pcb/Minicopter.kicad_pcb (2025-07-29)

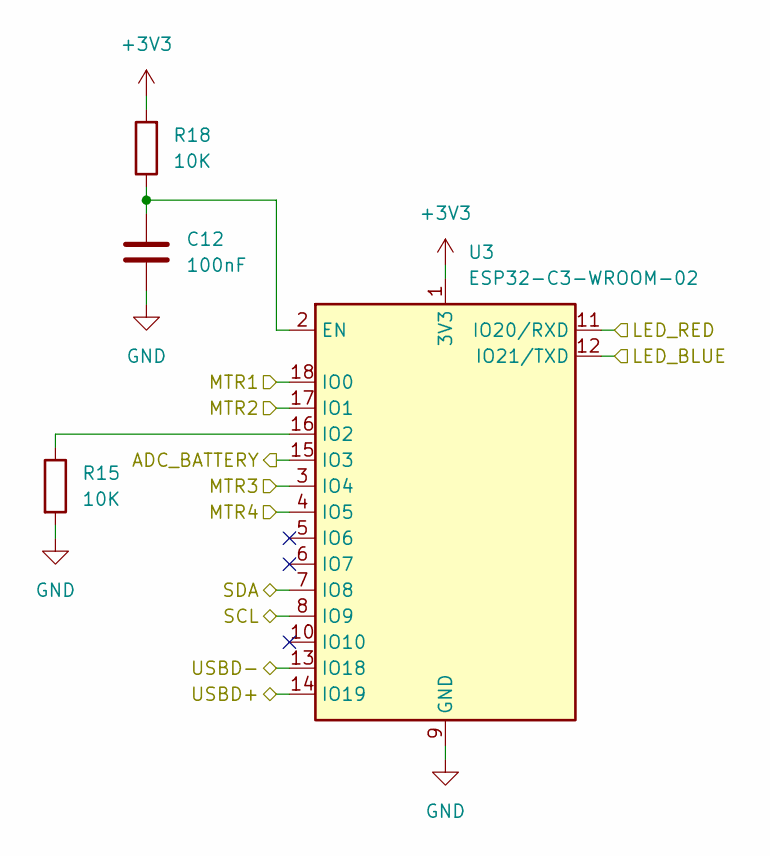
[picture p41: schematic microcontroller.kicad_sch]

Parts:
C12: 100nF; C_0603_1608Metric
R15, R18: 10K; R_0603_1608Metric
U3: ESP32-C3-WROOM-02

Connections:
+3V3: R18.2, U3.1 (3V3); also elsewhere on the board
/battery control/ADC_BATTERY: U3.15 (IO3); also elsewhere on the board
/microcontroller/LED_BLUE: U3.12 (IO21/TXD); also elsewhere on the board
/microcontroller/LED_RED: U3.11 (IO20/RXD); also elsewhere on the board
/microcontroller/MTR1: U3.18 (IO0); also elsewhere on the board
/microcontroller/MTR2: U3.17 (IO1); also elsewhere on the board
/microcontroller/MTR3: U3.3 (IO4); also elsewhere on the board
/microcontroller/MTR4: U3.4 (IO5); also elsewhere on the board
/microcontroller/SCL: U3.8 (IO9); also elsewhere on the board
/microcontroller/SDA: U3.7 (IO8); also elsewhere on the board
/microcontroller/USBD+: U3.14 (IO19); also elsewhere on the board
/microcontroller/USBD-: U3.13 (IO18); also elsewhere on the board
GND: C12.2, R15.2, U3.9 (GND), U3.19 (GND); also elsewhere on the board
unnamed: C12.1, R18.1, U3.2 (EN)
unnamed: R15.1, U3.16 (IO2)

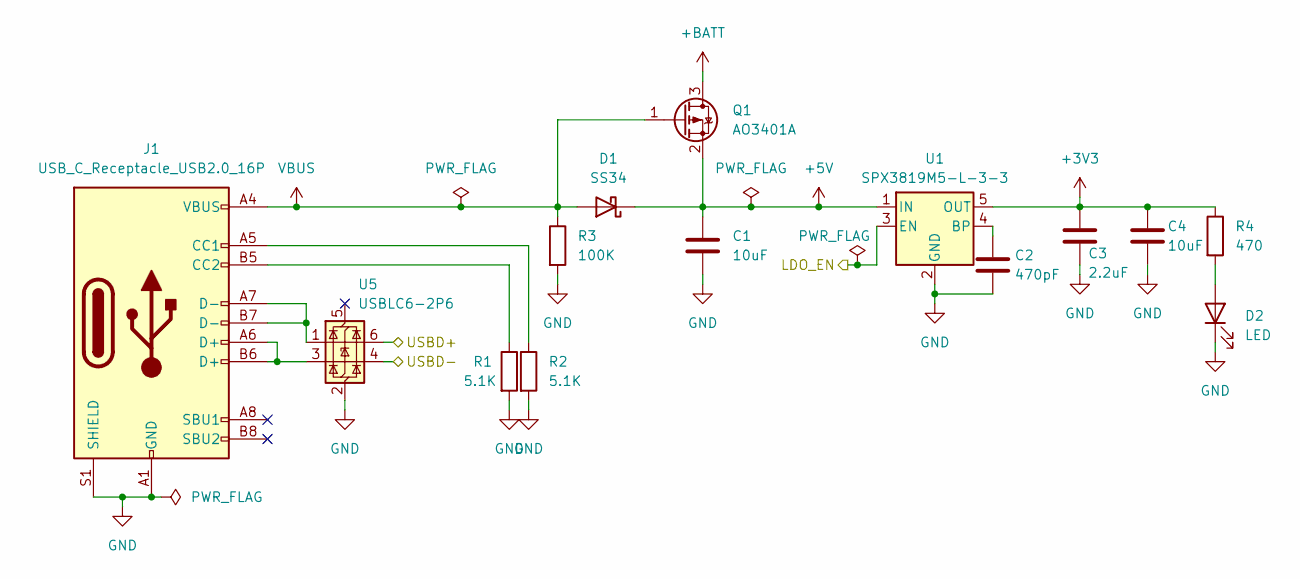
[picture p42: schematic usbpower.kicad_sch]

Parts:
C1, C4: 10uF; C_0603_1608Metric
C2: 470pF; C_0603_1608Metric
C3: 2.2uF; C_0603_1608Metric
D1: SS34; D_SMA
D2: LED; LED_0603_1608Metric
J1: USB_C_Receptacle_USB2.0_16P; USB_C_Receptacle_GCT_USB4085
Q1: AO3401A; SOT-23
R1, R2: 5.1K; R_0603_1608Metric
R3: 100K; R_0603_1608Metric
R4: 470; R_0603_1608Metric
U1: SPX3819M5-L-3-3; SOT-23-5
U5: USBLC6-2P6; SOT-666

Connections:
+3V3: C3.1, C4.1, R4.1, U1.5 (OUT); also elsewhere on the board
+5V: C1.1, D1.1 (K), Q1.2 (S), U1.1 (IN); also elsewhere on the board
+BATT: Q1.3 (D); also elsewhere on the board
/battery control/LDO_EN: U1.3 (EN); also elsewhere on the board
/microcontroller/USBD+: U5.6 (I/O1); also elsewhere on the board
/microcontroller/USBD-: U5.4 (I/O2); also elsewhere on the board
GND: C1.2, C2.2, C3.2, C4.2, D2.1 (K), J1.A1 (GND), J1.A12 (GND), J1.B1 (GND), J1.B12 (GND), J1.S1 (SHIELD), R1.2, R2.2, R3.2, U1.2 (GND), U5.2 (GND); also elsewhere on the board
unnamed: D2.2 (A), R4.2
unnamed: J1.A5 (CC1), R2.1
unnamed: J1.B5 (CC2), R1.1
unnamed: J1.A6 (D+), J1.B6 (D+), U5.3 (I/O2)
unnamed: J1.A7 (D-), J1.B7 (D-), U5.1 (I/O1)
unnamed: C2.1, U1.4 (BP)
VBUS: D1.2 (A), J1.A4 (VBUS), J1.A9 (VBUS), J1.B4 (VBUS), J1.B9 (VBUS), Q1.1 (G), R3.1; also elsewhere on the board

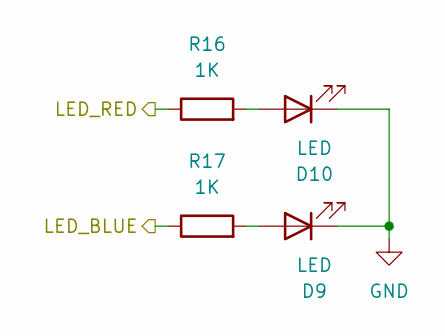
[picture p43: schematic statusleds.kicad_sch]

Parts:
D9, D10: LED; LED_0603_1608Metric
R16, R17: 1K; R_0603_1608Metric

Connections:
/microcontroller/LED_BLUE: R17.1; also elsewhere on the board
/microcontroller/LED_RED: R16.1; also elsewhere on the board
GND: D9.1 (K), D10.1 (K); also elsewhere on the board
unnamed: D9.2 (A), R17.2
unnamed: D10.2 (A), R16.2

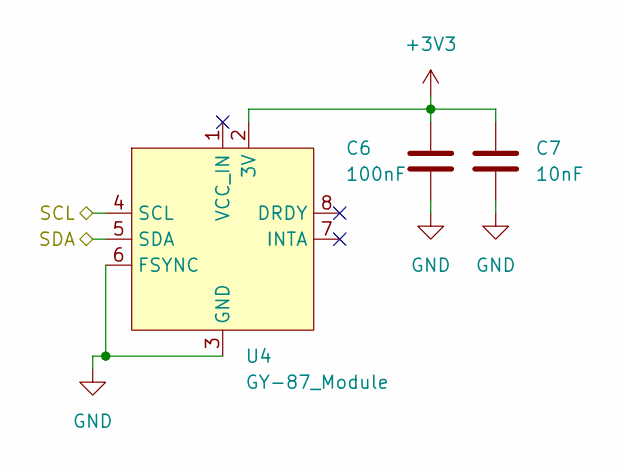
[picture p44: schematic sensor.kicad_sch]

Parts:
C6: 100nF; C_0603_1608Metric
C7: 10nF; C_0603_1608Metric
U4: GY-87_Module

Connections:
+3V3: C6.1, C7.1, U4.2 (3V); also elsewhere on the board
/microcontroller/SCL: U4.4 (SCL); also elsewhere on the board
/microcontroller/SDA: U4.5 (SDA); also elsewhere on the board
GND: C6.2, C7.2, U4.3 (GND), U4.6 (FSYNC); also elsewhere on the board

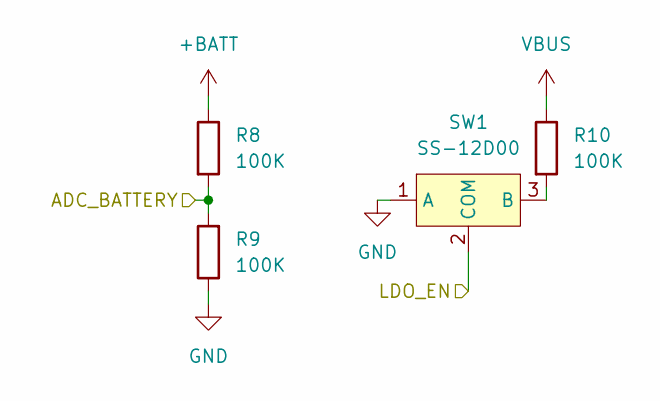
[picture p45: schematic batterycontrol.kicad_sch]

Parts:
R8, R9, R10: 100K; R_0603_1608Metric
SW1: SS-12D00; SS12-D00

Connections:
+BATT: R8.1; also elsewhere on the board
/battery control/ADC_BATTERY: R8.2, R9.2; also elsewhere on the board
/battery control/LDO_EN: SW1.2 (COM); also elsewhere on the board
GND: R9.1, SW1.1 (A); also elsewhere on the board
unnamed: R10.2, SW1.3 (B)
VBUS: R10.1; also elsewhere on the board

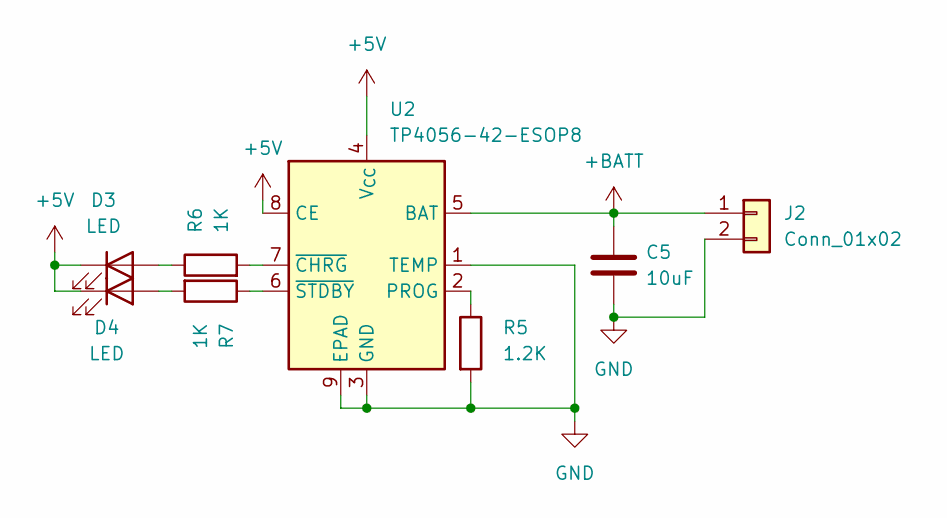
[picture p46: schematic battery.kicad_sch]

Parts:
C5: 10uF; C_0603_1608Metric
D3, D4: LED; LED_0603_1608Metric
J2: Conn_01x02; JST_PH_B2B-PH-SM4-TB_1x02-1MP_P2.00mm_Vertical
R5: 1.2K; R_0603_1608Metric
R6, R7: 1K; R_0603_1608Metric
U2: TP4056-42-ESOP8; SOIC-8-1EP_3.9x4.9mm_P1.27mm_EP2.41x3.3mm_ThermalVias

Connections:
+5V: D3.1 (K), D4.1 (K), U2.4 (V_{CC}), U2.8 (CE); also elsewhere on the board
+BATT: C5.1, J2.1, U2.5 (BAT); also elsewhere on the board
GND: C5.2, J2.2, R5.2, U2.1 (TEMP), U2.3 (GND), U2.9 (EPAD); also elsewhere on the board
unnamed: D3.2 (A), R6.1
unnamed: D4.2 (A), R7.2
unnamed: R5.1, U2.2 (PROG)
unnamed: R6.2, U2.7 (~CHRG)
unnamed: R7.1, U2.6 (~STDBY)

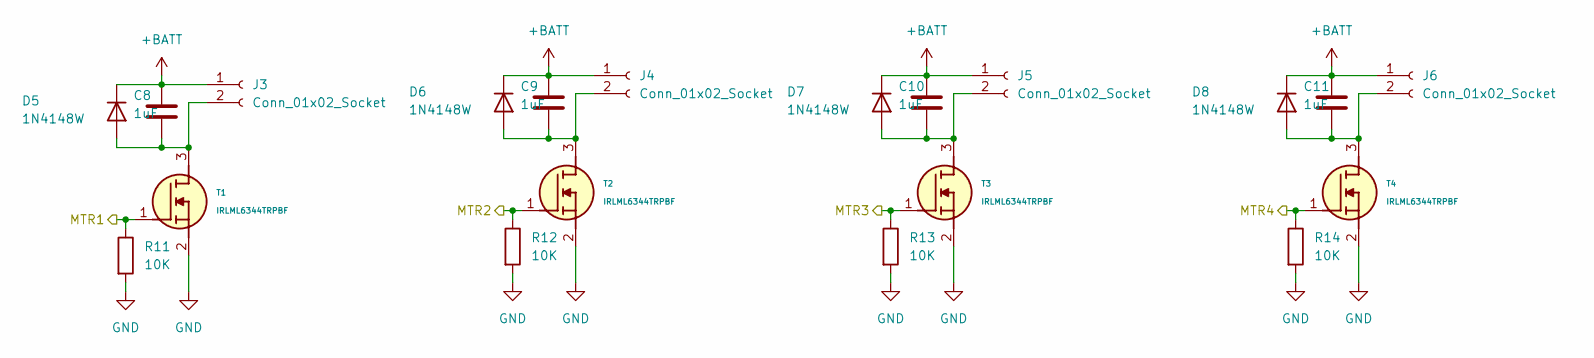
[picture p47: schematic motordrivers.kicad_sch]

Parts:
C8, C9, C10, C11: 1uF; C_0603_1608Metric
D5, D6, D7, D8: 1N4148W; D_SOD-123
J3, J4, J5, J6: Conn_01x02_Socket; JST_GH_BM02B-GHS-TBT_1x02-1MP_P1.25mm_Vertical
R11, R12, R13, R14: 10K; R_0603_1608Metric
T1, T2, T3, T4: IRLML6344TRPBF; MFR.Part # IRLML6344TRPBF-HXY; LCSC Part # C6285738

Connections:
+BATT: C8.1, C9.1, C10.1, C11.1, D5.1 (K), D6.1 (K), D7.1 (K), D8.1 (K), J3.1, J4.1, J5.1, J6.1; also elsewhere on the board
/microcontroller/MTR1: R11.1, T1.1 (G); also elsewhere on the board
/microcontroller/MTR2: R12.1, T2.1 (G); also elsewhere on the board
/microcontroller/MTR3: R13.1, T3.1 (G); also elsewhere on the board
/microcontroller/MTR4: R14.1, T4.1 (G); also elsewhere on the board
GND: R11.2, R12.2, R13.2, R14.2, T1.2 (S), T2.2 (S), T3.2 (S), T4.2 (S); also elsewhere on the board
unnamed: C8.2, D5.2 (A), J3.2, T1.3 (D)
unnamed: C9.2, D6.2 (A), J4.2, T2.3 (D)
unnamed: C10.2, D7.2 (A), J5.2, T3.3 (D)
unnamed: C11.2, D8.2 (A), J6.2, T4.3 (D)

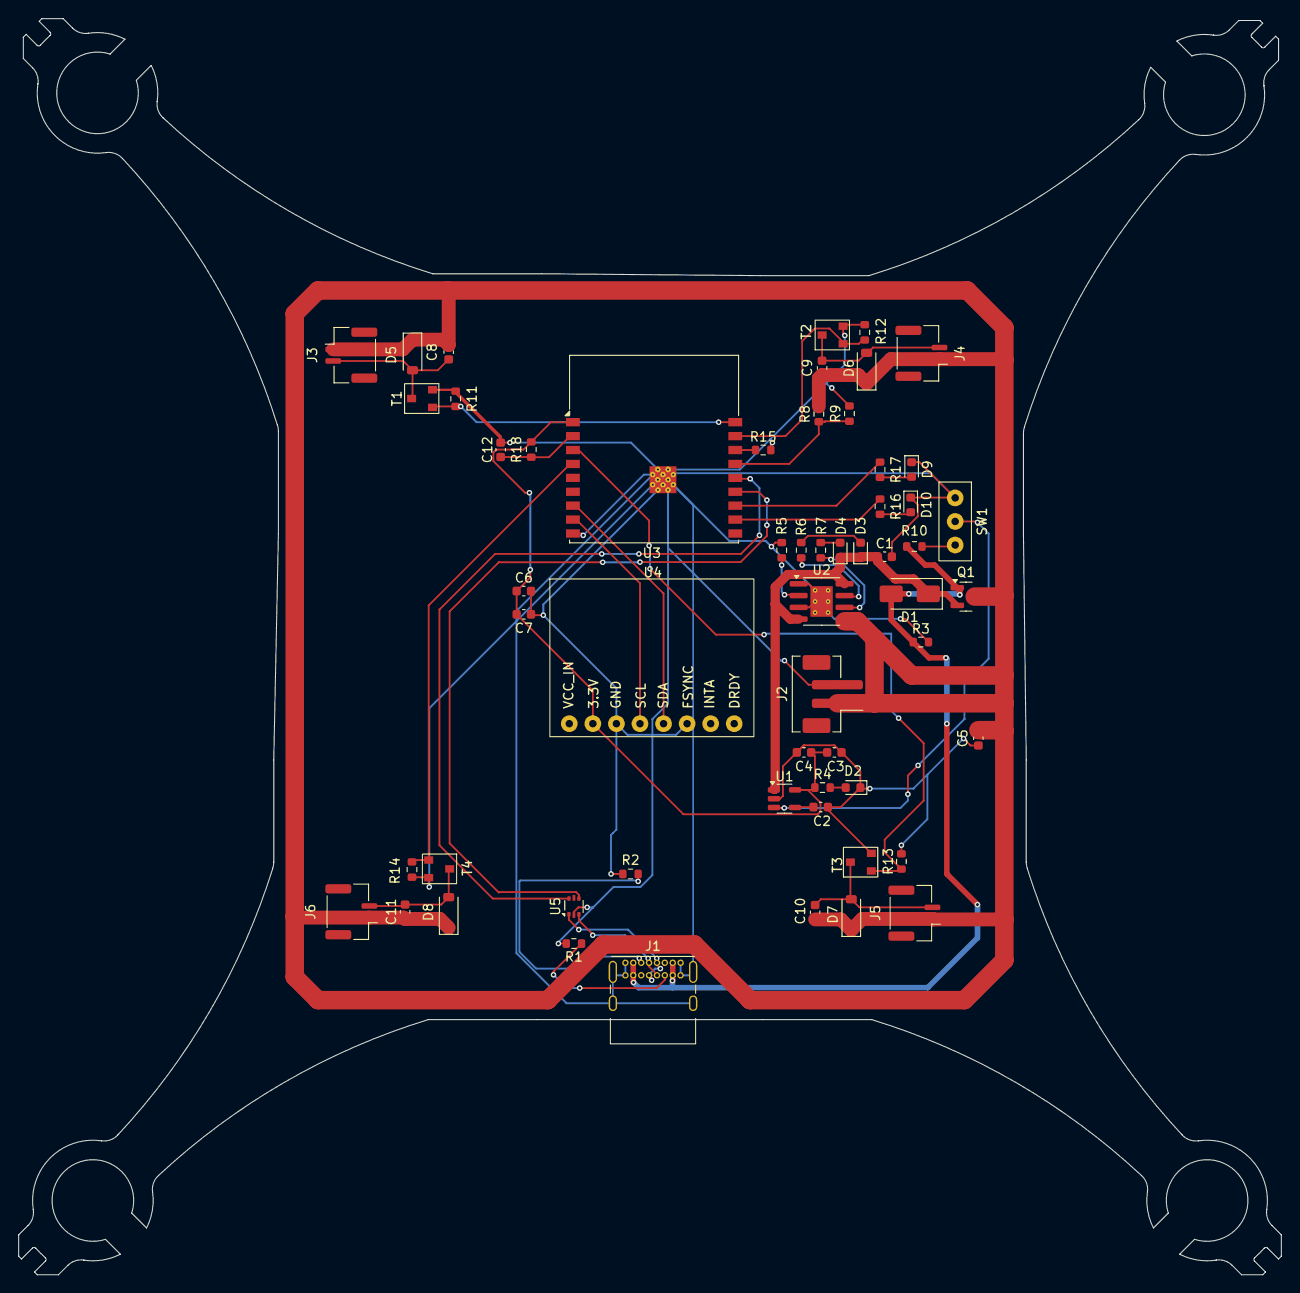
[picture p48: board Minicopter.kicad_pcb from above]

Board: 2 copper layers, 136.1 x 135.4 mm, 57 parts (0 on the bottom side), 37 nets.

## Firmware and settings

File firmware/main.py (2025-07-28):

from machine import Pin, PWM, I2C, ADC
import time
from MPU6050 import MPU6050
import bmp180

# motor
motor_pins = [18, 17, 3, 4]  # [FL, FR, BL, BR]
motors = [PWM(Pin(p), freq=20000, duty_u16=0) for p in motor_pins]

# batt
adc_battery = ADC(Pin(15))
adc_battery.atten(ADC.ATTN_11DB)

i2c = I2C(0, scl=Pin(8), sda=Pin(7))
time.sleep(1)
mpu = MPU6050(i2c)
bmp = bmp180.BMP085(i2c)

# pid
class PID:
    def __init__(self, Kp, Ki, Kd):
        self.Kp = Kp
        self.Ki = Ki
        self.Kd = Kd
        self.last_error = 0
        self.integral = 0

    def compute(self, target, current):
        error = target - current
        self.integral += error
        derivative = error - self.last_error
        self.last_error = error
        return self.Kp * error + self.Ki * self.integral + self.Kd * derivative

def mix_motors(throttle, pitch_corr, roll_corr, yaw_corr):
    motor_values = [0, 0, 0, 0]  # FL, FR, BL, BR
    motor_values[0] = throttle + pitch_corr + roll_corr - yaw_corr
    motor_values[1] = throttle + pitch_corr - roll_corr + yaw_corr
    motor_values[2] = throttle - pitch_corr + roll_corr + yaw_corr
    motor_values[3] = throttle - pitch_corr - roll_corr - yaw_corr

    for i in range(4):
        duty = int(max(min(motor_values[i], 100), 0) / 100 * 65535)
        motors[i].duty_u16(duty)

def read_battery_voltage():
    raw = adc_battery.read()
    voltage = (raw / 4095) * 3.3 * 2
    return voltage

pid_pitch = PID(1.2, 0.0, 0.3)
pid_roll = PID(1.2, 0.0, 0.3)
pid_yaw = PID(0.8, 0.0, 0.2)
pid_x = PID(0.6, 0.01, 0.2)
pid_y = PID(0.6, 0.01, 0.2)
pid_z = PID(1.0, 0.02, 0.3)

waypoints = [
    (0, 0, 1.0),
    (1, 0, 1.0),
    (1, 1, 1.2),
    (0, 1, 1.0),
    (0, 0, 0.5)
]

position = [0.0, 0.0, 0.0]
velocity = [0.0, 0.0, 0.0]
last_time = time.ticks_ms()

baseline_altitude = bmp.read_altitude()

def update_position(accel):
    global last_time, velocity, position
    now = time.ticks_ms()
    dt = time.ticks_diff(now, last_time) / 1000.0
    last_time = now

    for i, axis in enumerate(['x', 'y']):
        a = accel[axis]
        velocity[i] += a * dt
        position[i] += velocity[i] * dt

    position[2] = bmp.read_altitude() - baseline_altitude

print("init... waiting 5 seconds")
time.sleep(5)

for wp in waypoints:
    print("moving to:", wp)
    reached = False
    timeout = time.ticks_ms() + 10000

    while not reached and time.ticks_ms() < timeout:
        accel = mpu.get_accel_data()
        gyro = mpu.get_gyro_data()

        update_position(accel)

        x_corr = pid_x.compute(wp[0], position[0])
        y_corr = pid_y.compute(wp[1], position[1])
        z_corr = pid_z.compute(wp[2], position[2])

        pitch_corr = pid_pitch.compute(x_corr, accel['y'])
        roll_corr = pid_roll.compute(y_corr, accel['x'])
        yaw_corr = pid_yaw.compute(0, gyro['z'])

        base_throttle = 50 + z_corr
        mix_motors(base_throttle, pitch_corr, roll_corr, yaw_corr)

        print(f"pos: {position}, alt: {bmp.read_altitude():.2f}m, batt: {read_battery_voltage():.2f}V")
        time.sleep(0.1)

        if all(abs(position[i] - wp[i]) < 0.2 for i in range(3)):
            reached = True

print("landing")
for i in range(20):
    mix_motors(20 - i, 0, 0, 0)
    time.sleep(0.1)
mix_motors(0, 0, 0, 0)

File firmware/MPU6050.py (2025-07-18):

"""This program handles the communication over I2C
between a Raspberry Pi and a MPU-6050 Gyroscope / Accelerometer combo.
Made by: MrTijn/Tijndagamer
Released under the MIT License
Copyright 2015
"""

import smbus3

class MPU6050:

    # Global Variables
    GRAVITIY_MS2 = 9.80665
    address = None
    bus = smbus3.SMBus(1)

    # Scale Modifiers
    ACCEL_SCALE_MODIFIER_2G = 16384.0
    ACCEL_SCALE_MODIFIER_4G = 8192.0
    ACCEL_SCALE_MODIFIER_8G = 4096.0
    ACCEL_SCALE_MODIFIER_16G = 2048.0

    GYRO_SCALE_MODIFIER_250DEG = 131.0
    GYRO_SCALE_MODIFIER_500DEG = 65.5
    GYRO_SCALE_MODIFIER_1000DEG = 32.8
    GYRO_SCALE_MODIFIER_2000DEG = 16.4

    # Pre-defined ranges
    ACCEL_RANGE_2G = 0x00
    ACCEL_RANGE_4G = 0x08
    ACCEL_RANGE_8G = 0x10
    ACCEL_RANGE_16G = 0x18

    GYRO_RANGE_250DEG = 0x00
    GYRO_RANGE_500DEG = 0x08
    GYRO_RANGE_1000DEG = 0x10
    GYRO_RANGE_2000DEG = 0x18

    # MPU-6050 Registers
    PWR_MGMT_1 = 0x6B
    PWR_MGMT_2 = 0x6C

    SELF_TEST_X = 0x0D
    SELF_TEST_Y = 0x0E
    SELF_TEST_Z = 0x0F
    SELF_TEST_A = 0x10

    ACCEL_XOUT0 = 0x3B
    ACCEL_XOUT1 = 0x3C
    ACCEL_YOUT0 = 0x3D
    ACCEL_YOUT1 = 0x3E
    ACCEL_ZOUT0 = 0x3F
    ACCEL_ZOUT1 = 0x40

    TEMP_OUT0 = 0x41
    TEMP_OUT1 = 0x42

    GYRO_XOUT0 = 0x43
    GYRO_XOUT1 = 0x44
    GYRO_YOUT0 = 0x45
    GYRO_YOUT1 = 0x46
    GYRO_ZOUT0 = 0x47
    GYRO_ZOUT1 = 0x48

    ACCEL_CONFIG = 0x1C
    GYRO_CONFIG = 0x1B

    def __init__(self, address):
        self.address = address

        # Wake up the MPU-6050 since it starts in sleep mode
        self.bus.write_byte_data(self.address, self.PWR_MGMT_1, 0x00)

    # I2C communication methods

    def read_i2c_word(self, register):
        """Read two i2c registers and combine them.

        register -- the first register to read from.
        Returns the combined read results.
        """
        # Read the data from the registers
        high = self.bus.read_byte_data(self.address, register)
        low = self.bus.read_byte_data(self.address, register + 1)

        value = (high << 8) + low

        if (value >= 0x8000):
            return -((65535 - value) + 1)
        else:
            return value

    # MPU-6050 Methods

    def get_temp(self):
        """Reads the temperature from the onboard temperature sensor of the MPU-6050.

        Returns the temperature in degrees Celcius.
        """
        # Get the raw data
        raw_temp = self.read_i2c_word(self.TEMP_OUT0)

        # Get the actual temperature using the formule given in the
        # MPU-6050 Register Map and Descriptions revision 4.2, page 30
        actual_temp = (raw_temp / 340) + 36.53

        # Return the temperature
        return actual_temp

    def set_accel_range(self, accel_range):
        """Sets the range of the accelerometer to range.

        accel_range -- the range to set the accelerometer to. Using a
        pre-defined range is advised.
        """
        # First change it to 0x00 to make sure we write the correct value later
        self.bus.write_byte_data(self.address, self.ACCEL_CONFIG, 0x00)

        # Write the new range to the ACCEL_CONFIG register
        self.bus.write_byte_data(self.address, self.ACCEL_CONFIG, accel_range)

    def read_accel_range(self, raw = False):
        """Reads the range the accelerometer is set to.

        If raw is True, it will return the raw value from the ACCEL_CONFIG
        register
        If raw is False, it will return an integer: -1, 2, 4, 8 or 16. When it
        returns -1 something went wrong.
        """
        # Get the raw value
        raw_data = self.bus.read_byte_data(self.address, self.ACCEL_CONFIG)

        if raw is True:
            return raw_data
        elif raw is False:
            if raw_data == self.ACCEL_RANGE_2G:
                return 2
            elif raw_data == self.ACCEL_RANGE_4G:
                return 4
            elif raw_data == self.ACCEL_RANGE_8G:
                return 8
            elif raw_data == self.ACCEL_RANGE_16G:
                return 16
            else:
                return -1

    def get_accel_data(self, g = False):
        """Gets and returns the X, Y and Z values from the accelerometer.

        If g is True, it will return the data in g
        If g is False, it will return the data in m/s^2
        Returns a dictionary with the measurement results.
        """
        # Read the data from the MPU-6050
        x = self.read_i2c_word(self.ACCEL_XOUT0)
        y = self.read_i2c_word(self.ACCEL_YOUT0)
        z = self.read_i2c_word(self.ACCEL_ZOUT0)

        accel_scale_modifier = None
        accel_range = self.read_accel_range(True)

        if accel_range == self.ACCEL_RANGE_2G:
            accel_scale_modifier = self.ACCEL_SCALE_MODIFIER_2G
        elif accel_range == self.ACCEL_RANGE_4G:
            accel_scale_modifier = self.ACCEL_SCALE_MODIFIER_4G
        elif accel_range == self.ACCEL_RANGE_8G:
            accel_scale_modifier = self.ACCEL_SCALE_MODIFIER_8G
        elif accel_range == self.ACCEL_RANGE_16G:
            accel_scale_modifier = self.ACCEL_SCALE_MODIFIER_16G
        else:
            print("Unkown range - accel_scale_modifier set to self.ACCEL_SCALE_MODIFIER_2G")
            accel_scale_modifier = self.ACCEL_SCALE_MODIFIER_2G

        x = x / accel_scale_modifier
        y = y / accel_scale_modifier
        z = z / accel_scale_modifier

        if g is True:
            return {'x': x, 'y': y, 'z': z}
        elif g is False:
            x = x * self.GRAVITIY_MS2
            y = y * self.GRAVITIY_MS2
            z = z * self.GRAVITIY_MS2
            return {'x': x, 'y': y, 'z': z}

    def set_gyro_range(self, gyro_range):
        """Sets the range of the gyroscope to range.

        gyro_range -- the range to set the gyroscope to. Using a pre-defined
        range is advised.
        """
        # First change it to 0x00 to make sure we write the correct value later
        self.bus.write_byte_data(self.address, self.GYRO_CONFIG, 0x00)

        # Write the new range to the ACCEL_CONFIG register
        self.bus.write_byte_data(self.address, self.GYRO_CONFIG, gyro_range)

    def read_gyro_range(self, raw = False):
        """Reads the range the gyroscope is set to.

        If raw is True, it will return the raw value from the GYRO_CONFIG
        register.
        If raw is False, it will return 250, 500, 1000, 2000 or -1. If the
        returned value is equal to -1 something went wrong.
        """
        # Get the raw value
        raw_data = self.bus.read_byte_data(self.address, self.GYRO_CONFIG)
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

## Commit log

2025-07-08 power schem
    [Minicopter.kicad_pcb, Minicopter.kicad_sch, battery.kicad_sch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]
2025-07-09 with errors
    [Minicopter.kicad_sch, batterycontrol.kicad_sch, microcontroller.kicad_sch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]
2025-07-09 finished schematic
    [Minicopter.kicad_sch, battery.kicad_sch, batterycontrol.kicad_sch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]
2025-07-10 schematic done
    [battery.kicad_sch, batterycontrol.kicad_sch, microcontroller.kicad_sch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]
2025-07-16 without gnd
    [Minicopter.kicad_pcb, usbpower.kicad_sch]
2025-07-18 oops now done hopefully
    [Minicopter.kicad_pcb, Minicopter.step]
2025-07-22 update bom
    [Minicopter BOM.csv, Minicopter.kicad_pcb]
2025-07-25 update bom:
    [Minicopter BOM.csv]
2025-07-27 price went up :pensive:
    [Minicopter BOM.csv]
2025-07-27 Revert "price went up :pensive:"
    This reverts commit 4fa7545903ad4b724715b33760c9a4a9f241c5e7.
    [Minicopter BOM.csv]
2025-07-29 fixed usb placement
    [Minicopter.kicad_pcb]
2025-08-15 assembly progress
